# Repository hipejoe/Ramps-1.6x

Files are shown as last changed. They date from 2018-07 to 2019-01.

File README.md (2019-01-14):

Ramps-1.6 or so
===========

forked from ultimachine/Ramps 1.4

terminated AUX doe to space

added libs for tmc2130 watterot with conf0 installed 
add E2
chanded libs f tmc2130 to not use space of unused headers
added supression to endstops but removed 2nd endstop for axis (has tmc2130 so only Z and probe may need one.
re added 2servos
upgraded to 4thermoistors

integrated my previous fan extendr to 5 external outputs
removed VIN (toDO! check arduinos power consumption etc)
changed package or reset + external reset 

changed few Packages to match order
Orderd First Batch PCBs to test

RAMPS 1.6.3 
Got one wirestumb on Zmin fixed
Changed Pins Back to HWSPI 
Added I2C pin Header and HW SPI breakout
added 5vin 

Current status: all up and running thermistors are and endstops are "noisefree" printe is running it for 5month now, got some PCBs left..

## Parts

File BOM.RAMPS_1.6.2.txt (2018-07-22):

Stückliste exportiert aus D:/Documents/PCB/eagle/eagle/proj/RAMTPB/Ramps-1.4.2-master/RAMPS_1.6.2.sch am 22.07.2018 23:47

Qty Value               Device                  Package                      Parts                         Description                                                                                                     MF MPN OC_FARNELL OC_NEWARK SF_ID     SPICEPREFIX
4                       2,15/1,0                2,15/1,0                     +12, +24, G12, GND            THROUGH-HOLE PAD                                                                                                                                                 
3                       3PIN-HEADER             3PIN-HEADER                  X-, Y-, Z-                    PIN HEADER                                                                                                                                                       
3                       CONN_022.54MM_SCREWTERM 1X02_2.54_SCREWTERM          HEAT1, HEAT2, HEAT3           Multi connection point. Often used as Generic Header-pin footprint for 0.1 inch spaced/style header connections                                                  
4                       CONN_02LOCK             1X02_LOCK                    T0, T1, T2, T3                Multi connection point. Often used as Generic Header-pin footprint for 0.1 inch spaced/style header connections                                                  
6                       CONN_02POLAR_LOCK       MOLEX-1X2_LOCK               EX0, EX1, EX2, EX3, EX4, RSET Multi connection point. Often used as Generic Header-pin footprint for 0.1 inch spaced/style header connections                             PRT-09918 B          
2                       CONN_03                 1X03                         SERV0, SERV1                  Multi connection point. Often used as Generic Header-pin footprint for 0.1 inch spaced/style header connections                                                  
5                       NMOSSOT223              SOT223                       TEX0, TEX1, TEX2, TEX3, TEX4  MOS FET                                                                                                                unknown    unknown             J          
3   1.8K                R-US_R1206              R1206                        R23, R24, R25                 RESISTOR, American symbol                                                                                                                                        
5   1.8K                R-US_R1206              R1206                        R20, R28, R31, R34, R37       RESISTOR, American symbol                                                                                                                             R          
5   10                  R-US_R1206              R1206                        R18, R26, R29, R32, R35       RESISTOR, American symbol                                                                                                                             R          
1   100K                R-US_R1206              R1206                        R19                           RESISTOR, American symbol                                                                                                                             L          
4   100K                R-US_R1206              R1206                        R27, R30, R33, R36            RESISTOR, American symbol                                                                                                                             R          
3   100k                R-US_R1206              R1206                        R2, R4, R9                    RESISTOR, American symbol                                                                                                                                        
1   100nF               C-EUC1206               C1206                        C2                            CAPACITOR, European symbol                                                                                                                                       
7   100uF               CPOL-US153CLV-0605      153CLV-0605                  C3, C4, C6, C7, C9, C10, C17  POLARIZED CAPACITOR, American symbol                                                                                                                             
6   10k                 R-US_R1206              R1206                        R3, R5, R6, R8, R10, R16      RESISTOR, American symbol                                                                                                                                        
3   10r                 R-US_R1206              R1206                        R13, R14, R15                 RESISTOR, American symbol                                                                                                                                        
3   10uF                C-EUC1206               C1206                        C11, C13, C15                 CAPACITOR, European symbol                                                                                                                                       
4   10uF                CPOL-US153CLV-0405      153CLV-0405                  C1, C5, C8, C12               POLARIZED CAPACITOR, American symbol                                                                                                                             
1   1K                  R-US_R1206              R1206                        R12                           RESISTOR, American symbol                                                                                                                                        
2   1N4004              1N4004                  DO41-10                      D2, D3                        DIODE                                                                                                                                                            
4   4.7K                R-US_R1206              R1206                        R1, R7, R11, R17              RESISTOR, American symbol                                                                                                                                        
1   ARDUINOSHIELD       ARDUINOSHIELD           REPRAPJR_ARDUINO_MEGA_SHIELD U$1                           aus schaltplan kopierte version von amega                                                                                                                        
2   SMD-AUTOMOTIVE-FUSE SMD-AUTOMOTIVE-FUSE     BLADEFUSE                    F1, F2                        Surface mount fuse holder for kfz blade fuses                                                                                                                    
3   STP55NF06L          IRF512                  TO220BV                      Q1, Q2, Q3                    N-CHANNEL MOS FET                                                                                                                                                
6   TMC2130DIAG         TMC2130DIAG             TMC2130DIAG0                 E0, E1, E2, X, Y, Z                                                                                                                                                                            
1   green               LEDCHIPLED_1206         CHIPLED_1206                 LED1                          LED                                                                                                                                                              
3   red                 LEDCHIPLED_1206         CHIPLED_1206                 LED10, LEDD8, LEDD9           LED                                                                                                                                                              
5   red                 LEDCHIPLED_1206         CHIPLED_1206                 LED5, LED6, LED7, LED8, LED9  LED                                                                                                                                                   L          
1   reset               SKHMPWE010              SKHMPXE010                   S2                            6.2 X 6.5mm TACT Switch (SMD)

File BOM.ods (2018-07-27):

Qty | Value | Device | Package | Parts names | artNR | wo
4 |  | 2,15/1,0 | 2,15/1,0 | +12, +24, G12, GND
3 |  | 3PIN-HEADER | 3PIN-HEADER | X-, Y-, Z-
3 |  | CONN_022.54MM_SCREWTERM | 1X02_2.54_SCREWTERM | HEAT1, HEAT2, HEAT3
4 |  | CONN_02LOCK | 1X02_LOCK | T0, T1, T2, T3
6 |  | CONN_02POLAR_LOCK | MOLEX-1X2_LOCK | EX0, EX1, EX2, EX3, EX4, RSET
2 |  | CONN_03 | 1X03 | SERV0, SERV1
5 |  | NMOSSOT223 | SOT223 | TEX0, TEX1, TEX2, TEX3, TEX4 | ZVN 2106 G | rs | 0,45 | 2,25
8 | 1.8K | R-US_R1206 | R1206 | R20, R23, R24, R25, R28, R31, R34, R37 | RND 1206 1 1,8K | rs | 0,02 | 0,16
8 | 10ohm | R-US_R1206 | R1206 | R18, R26, R29, R32, R35 | RND 1206 1 10 | rs | 0,02 | 0,16
6 | 10k | R-US_R1206 | R1206 | R3, R5, R6, R8, R10, R16 | RND 1206 1 10K | rs | 0,02 | 0,12
4 | 4.7K | R-US_R1206 | R1206 | R1, R7, R11, R17 | RND 1206 1 4,7K | rs | 0,02 | 0,08
1 | 1K | R-US_R1206 | R1206 | R12 | RND 1206 1 1,1K | rs | 0,02 | 0,02
8 | 100K | R-US_R1206 | R1206 | R19, R27, R30, R33, R36 | RND 1206 1 100k | rs | 0,02 | 0,16
1 | 100nF | C-EUC1206 | C1206 | C2 | X7R 1206FCF 100N | rs | 0,04 | 0,04
7 | 100uF | CPOL-US153CLV-0605 | 153CLV-0605 6,3x5,6 | C3, C4, C6, C7, C9, C10, C17 | HA-V 100U 35 | rs | 0,28 | 1,96
3 | 10uF | C-EUC1206 | C1206 | C11, C13, C15 | Y5V 1206 DC 10U | rs | 0,04 | 0,12
4 | 10uF | CPOL-US153CLV-0405 | 153CLV-0405 4+5,6mm | C1, C5, C8, C12 | HA-V 10U 35-2 | rs | 0,16 | 0,64
2 | 1N4004 | 1N4004 | DO201 | D2, D3 | UF 5404 | rs | 0,15 | 0,3
1 | ARDUINOSHIELD | ARDUINOSHIELD | REPRAPJR_ARDUINO_MEGA_SHIELD | U$1 |  |  |  | 0
2 | SMD-AUTOMOTIVE-FUSEREICHELTVARIANTE | SMD-AUTOMOTIVE-FUSEREICHELTVARIANTE | RS-SMDFUSE | F1, F2 | IMAXX H1810-2X4 | rs | 0,93 | 1,86
3 | STP55NF06L | IRF512 | TO220BV | Q1, Q2, Q3 | IRLB 8721 | rs | 0,61 | 1,83
6 | TMC2130DIAG | TMC2130DIAG | TMC2130DIAG0 | E0, E1, E2, X, Y, Z |  |  |  | 0
1 | green | LEDCHIPLED_1206 | CHIPLED_1206 | LED1 | RND 135-00053 | rs | 0,06 | 0,06
8 | red | LEDCHIPLED_1206 | CHIPLED_1206 | LED5, LED6, LED7, LED8, LED9, LED10, LEDD8, LEDD9 | RND 135-00054 | rs | 0,06 | 0,48
1 | reset | SKHMPWE010 | SKHMPXE010 | S2 | TASTER 9315 | rs | 0,16 | 0,16
 |  |  |  |  |  |  |  | 10,4

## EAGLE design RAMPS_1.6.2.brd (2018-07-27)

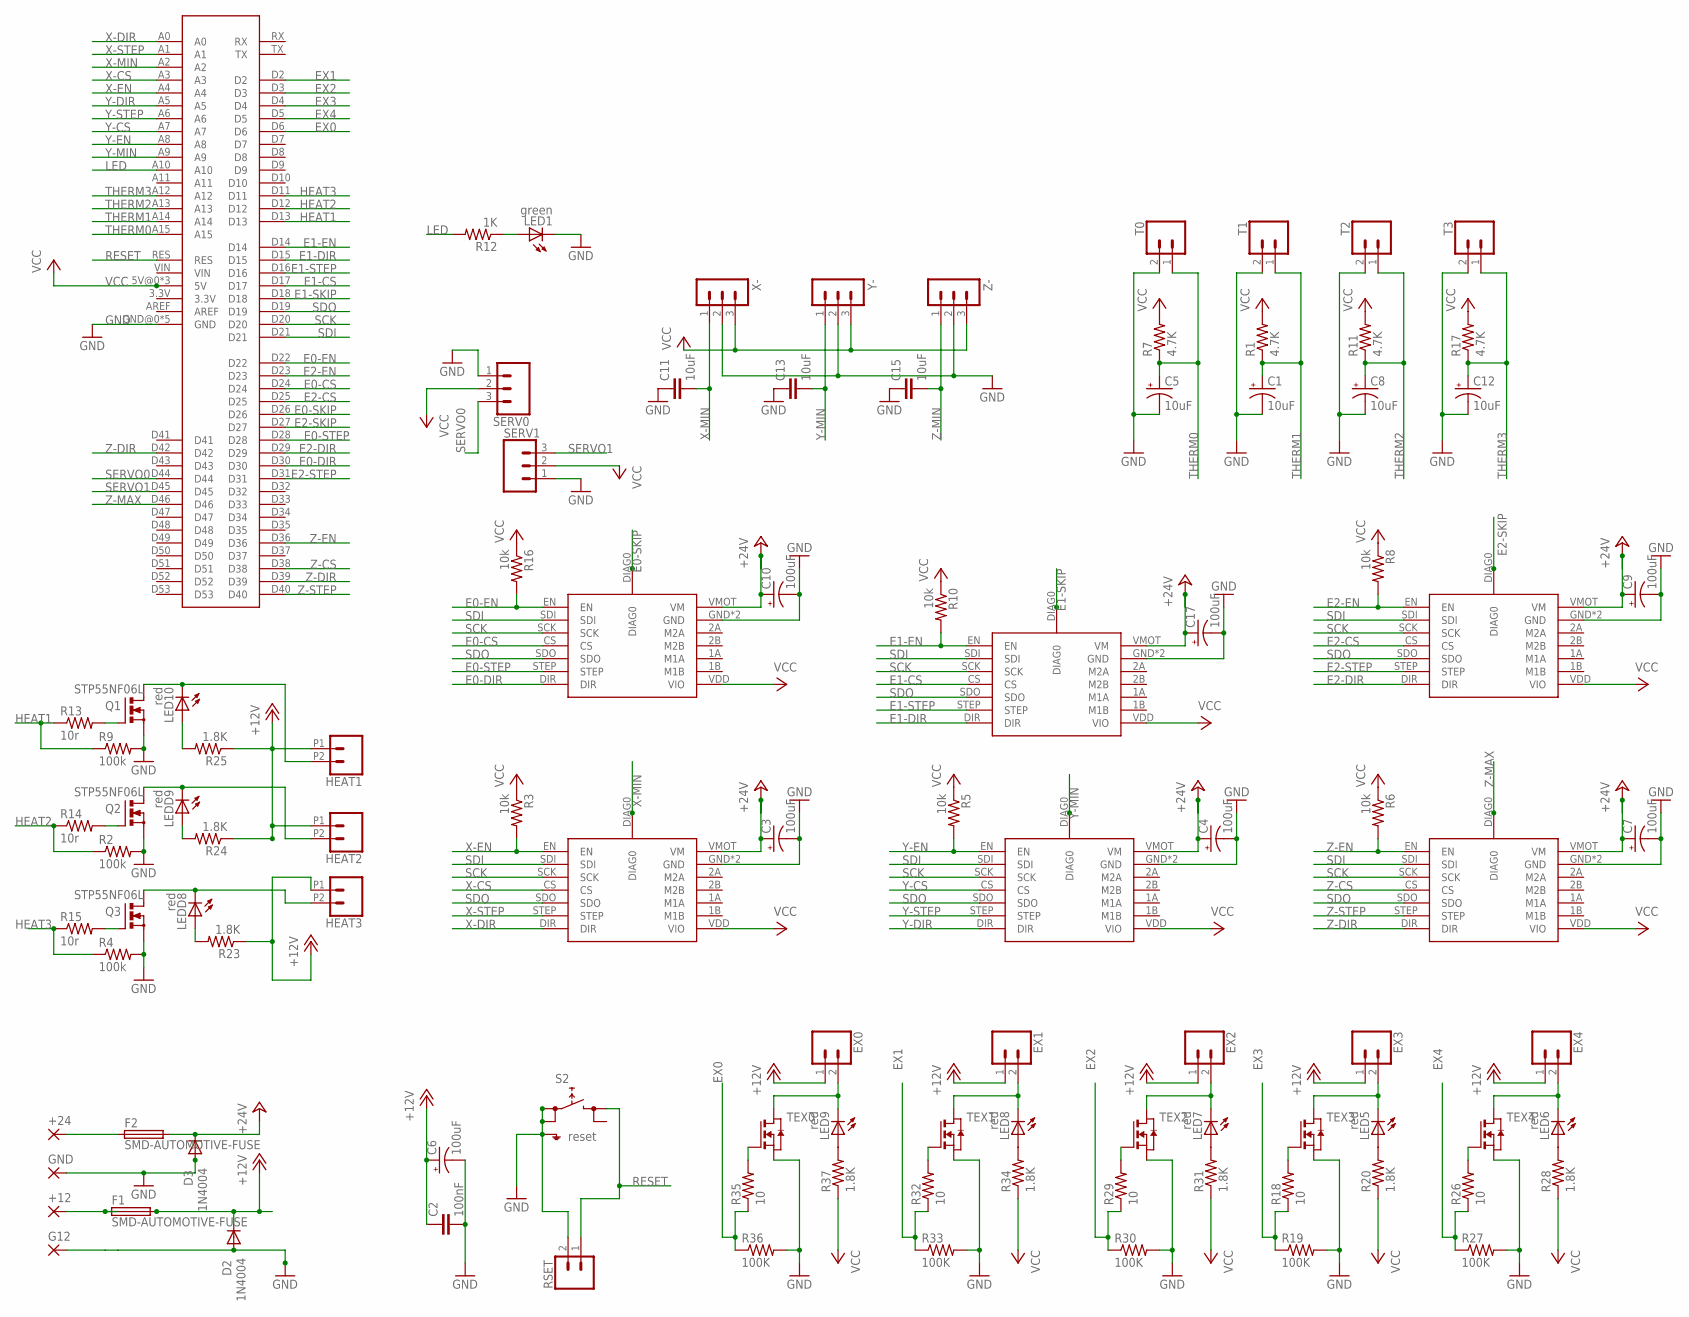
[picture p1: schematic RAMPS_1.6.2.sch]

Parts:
+12, +24: 2,15/1,0
C1, C5, C8, C12: 10uF; 153CLV-0405
C2: 100nF; C1206
C3, C4, C6, C7, C9, C10, C17: 100uF; 153CLV-0605
C11, C13, C15: 10uF; C1206
D2, D3: 1N4004; DO41-10
E0, E1, E2: TMC2130DIAG; TMC2130DIAG0
EX0, EX1, EX2, EX3, EX4: CONN_02POLAR_LOCK; MOLEX-1X2_LOCK
F1, F2: SMD-AUTOMOTIVE-FUSE; BLADEFUSE
G12: 2,15/1,0
GND: 2,15/1,0
HEAT1, HEAT2, HEAT3: CONN_022.54MM_SCREWTERM; 1X02_2.54_SCREWTERM
LED1: green; CHIPLED_1206
LED5, LED6, LED7, LED8, LED9, LED10: red; CHIPLED_1206
LEDD8, LEDD9: red; CHIPLED_1206
Q1, Q2, Q3: STP55NF06L; TO220BV
R1, R7, R11, R17: 4.7K; R1206
R2, R4, R9: 100k; R1206
R3, R5, R6, R8, R10, R16: 10k; R1206
R12: 1K; R1206
R13, R14, R15: 10r; R1206
R18, R26, R29, R32, R35: 10; R1206
R19, R27, R30, R33, R36: 100K; R1206
R20, R23, R24, R25, R28, R31, R34, R37: 1.8K; R1206
RSET: CONN_02POLAR_LOCK; MOLEX-1X2_LOCK
S2: reset; SKHMPXE010
SERV0, SERV1: CONN_03; 1X03
T0, T1, T2, T3: CONN_02LOCK; 1X02_LOCK
TEX0, TEX1, TEX2, TEX3, TEX4: NMOSSOT223; SOT223
U$1: ARDUINOSHIELD; REPRAPJR_ARDUINO_MEGA_SHIELD
X: TMC2130DIAG; TMC2130DIAG0
X-: 3PIN-HEADER
Y: TMC2130DIAG; TMC2130DIAG0
Y-: 3PIN-HEADER
Z: TMC2130DIAG; TMC2130DIAG0
Z-: 3PIN-HEADER

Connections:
+12V: C2.1, C6.+, D2.C, EX0.1, EX1.1, EX2.1, EX3.1, EX4.1, F1.2, F1.P$5, F1.P$6, F1.P$7, F1.P$8, HEAT1.P1 (1), HEAT2.P1 (1), HEAT3.P1 (1), R23.1, R24.1, R25.1
+24V: C3.+, C4.+, C7.+, C9.+, C10.+, C17.+, D3.C, E0.VMOT (VM), E1.VMOT (VM), E2.VMOT (VM), F2.2, F2.P$5, F2.P$6, F2.P$7, F2.P$8, X.VMOT (VM), Y.VMOT (VM), Z.VMOT (VM)
E0-CS: E0.CS, U$1.D24
E0-DIR: E0.DIR, U$1.D30
E0-EN: E0.EN, R16.2, U$1.D22
E0-SKIP: E0.DIAG0, U$1.D26
E0-STEP: E0.STEP, U$1.D28
E1-CS: E1.CS, U$1.D17
E1-DIR: E1.DIR, U$1.D15
E1-EN: E1.EN, R10.2, U$1.D14
E1-SKIP: E1.DIAG0, U$1.D18
E1-STEP: E1.STEP, U$1.D16
E2-CS: E2.CS, U$1.D25
E2-DIR: E2.DIR, U$1.D29
E2-EN: E2.EN, R8.2, U$1.D23
E2-SKIP: E2.DIAG0, U$1.D27
E2-STEP: E2.STEP, U$1.D31
EX0: R35.1, R36.1, U$1.D6
EX1: R32.1, R33.1, U$1.D2
EX2: R29.1, R30.1, U$1.D3
EX3: R18.1, R19.1, U$1.D4
EX4: R26.1, R27.1, U$1.D5
GND: C1.-, C2.2, C3.-, C4.-, C5.-, C6.-, C7.-, C8.-, C9.-, C10.-, C11.1, C12.-, C13.1, C15.1, C17.-, D2.A, D3.A, E0.GND, E0.GND@0 (GND), E1.GND, E1.GND@0 (GND), E2.GND, E2.GND@0 (GND), G12.1, GND.1, LED1.C, Q1.S, Q2.S, Q3.S, R2.2, R4.2, R9.2, R19.2, R27.2, R30.2, R33.2, R36.2, RSET.2, S2.1 (1.1), S2.2 (1.2), SERV0.1, SERV1.1, T0.2, T1.2, T2.2, T3.2, TEX0.3 (S), TEX1.3 (S), TEX2.3 (S), TEX3.3 (S), TEX4.3 (S), U$1.GND@0 (GND), U$1.GND@1 (GND), U$1.GND@2 (GND), U$1.GND@3 (GND), U$1.GND@4 (GND), X.GND, X.GND@0 (GND), X-.2, Y.GND, Y.GND@0 (GND), Y-.2, Z.GND, Z.GND@0 (GND), Z-.2; also elsewhere on the board
HEAT1: R9.1, R13.1, U$1.D13
HEAT2: R2.1, R14.1, U$1.D12
HEAT3: R4.1, R15.1, U$1.D11
LED: R12.2, U$1.A10
unnamed: HEAT2.P2 (2), LEDD9.C, Q2.D
unnamed: R18.2, TEX3.1 (G)
unnamed: HEAT1.P2 (2), LED10.C, Q1.D
unnamed: EX3.2, LED5.C, TEX3.2 (D), TEX3.4 (D)
unnamed: LED5.A, R20.2
unnamed: EX2.2, LED7.C, TEX2.2 (D), TEX2.4 (D)
unnamed: R26.2, TEX4.1 (G)
unnamed: EX4.2, LED6.C, TEX4.2 (D), TEX4.4 (D)
unnamed: LEDD8.A, R23.2
unnamed: LED6.A, R28.2
unnamed: R29.2, TEX2.1 (G)
unnamed: LED7.A, R31.2
unnamed: R32.2, TEX1.1 (G)
unnamed: EX1.2, LED8.C, TEX1.2 (D), TEX1.4 (D)
unnamed: LED8.A, R34.2
unnamed: R35.2, TEX0.1 (G)
unnamed: LEDD9.A, R24.2
unnamed: LED1.A, R12.1
unnamed: Q2.G, R14.2
unnamed: Q1.G, R13.2
unnamed: Q3.G, R15.2
unnamed: LED10.A, R25.2
unnamed: HEAT3.P2 (2), LEDD8.C, Q3.D
unnamed: +24.1, F2.1, F2.P$1, F2.P$2, F2.P$3, F2.P$4
unnamed: +12.1, F1.1, F1.P$1, F1.P$2, F1.P$3, F1.P$4
unnamed: EX0.2, LED9.C, TEX0.2 (D), TEX0.4 (D)
unnamed: LED9.A, R37.2
RESET: RSET.1, S2.3 (2.1), U$1.RES; also elsewhere on the board
SCK: E0.SCK, E1.SCK, E2.SCK, U$1.D20, X.SCK, Y.SCK, Z.SCK
SDI: E0.SDI, E1.SDI, E2.SDI, U$1.D21, X.SDI, Y.SDI, Z.SDI
SDO: E0.SDO, E1.SDO, E2.SDO, U$1.D19, X.SDO, Y.SDO, Z.SDO
SERVO0: SERV0.3, U$1.D44
SERVO1: SERV1.3, U$1.D45
THERM0: C5.+, R7.1, T0.1, U$1.A15
THERM1: C1.+, R1.1, T1.1, U$1.A14
THERM2: C8.+, R11.1, T2.1, U$1.A13
THERM3: C12.+, R17.1, T3.1, U$1.A12
VCC: E0.VDD (VIO), E1.VDD (VIO), E2.VDD (VIO), R1.2, R3.1, R5.1, R6.1, R7.2, R8.1, R10.1, R11.2, R16.1, R17.2, R20.1, R28.1, R31.1, R34.1, R37.1, SERV0.2, SERV1.2, U$1.5V@0 (5V), U$1.5V@1 (5V), U$1.5V@2 (5V), X.VDD (VIO), X-.3, Y.VDD (VIO), Y-.3, Z.VDD (VIO), Z-.3
X-CS: U$1.A3, X.CS
X-DIR: U$1.A0, X.DIR
X-EN: R3.2, U$1.A4, X.EN
X-MIN: C11.2, U$1.A2, X.DIAG0, X-.1
X-STEP: U$1.A1, X.STEP
Y-CS: U$1.A7, Y.CS
Y-DIR: U$1.A5, Y.DIR
Y-EN: R5.2, U$1.A8, Y.EN
Y-MIN: C13.2, U$1.A9, Y.DIAG0, Y-.1
Y-STEP: U$1.A6, Y.STEP
Z-CS: U$1.D38, Z.CS
Z-DIR: U$1.D39, U$1.D42, Z.DIR
Z-EN: R6.2, U$1.D36, Z.EN
Z-MAX: U$1.D46, Z.DIAG0
Z-MIN: C15.2, Z-.1
Z-STEP: U$1.D40, Z.STEP

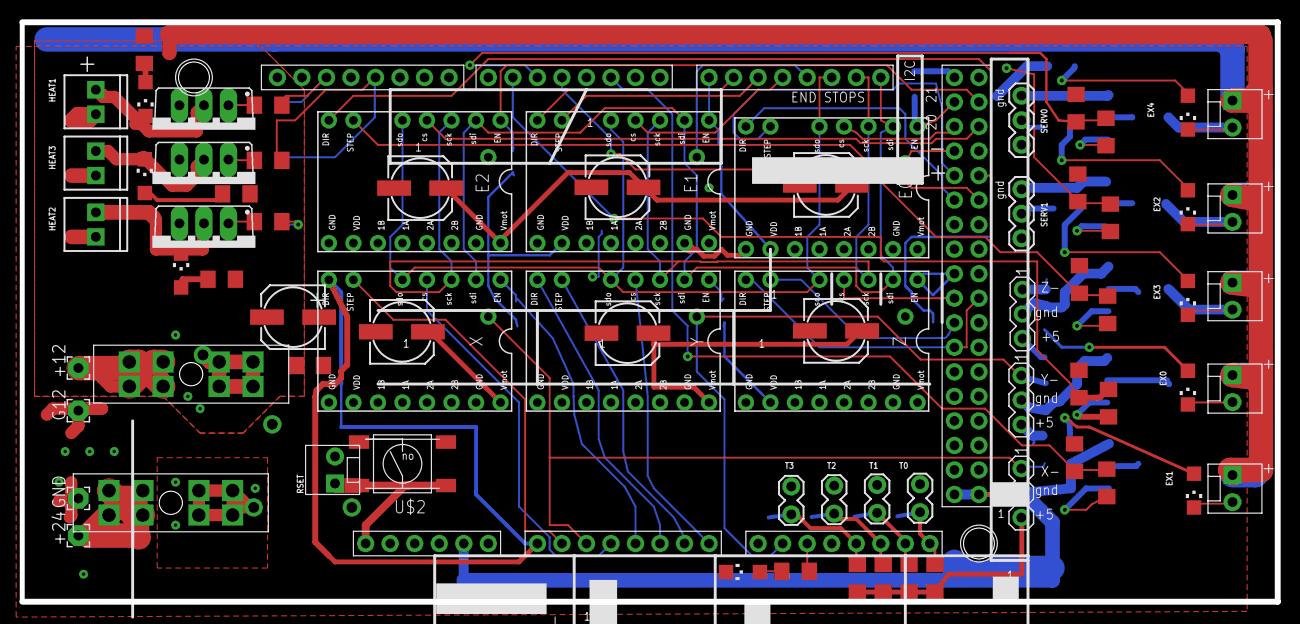
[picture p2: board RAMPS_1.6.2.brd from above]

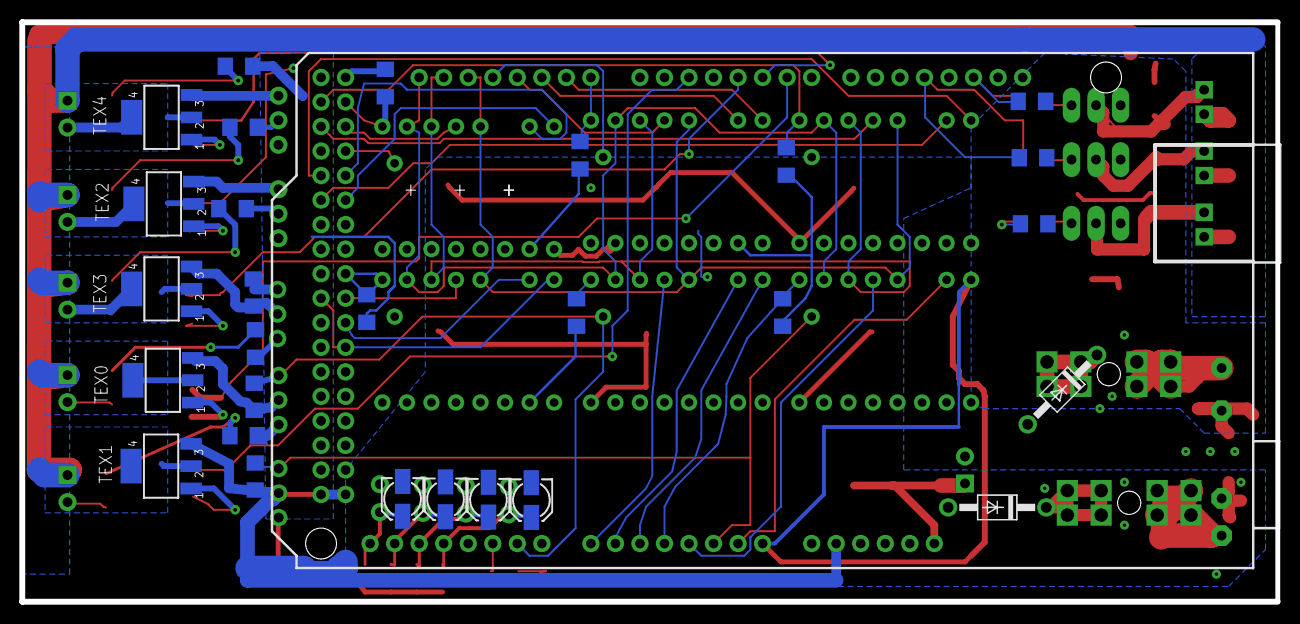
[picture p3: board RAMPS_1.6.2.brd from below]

Board: 4 copper layers, 130.0 x 60.0 mm, 101 parts (28 on the bottom side), 81 nets.

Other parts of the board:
U$2: RS-TASTER; RS-SWITCH

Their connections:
GND: U$2.P$1, U$2.P$2; also elsewhere on the board
RESET: U$2.P$3, U$2.P$4; also elsewhere on the board

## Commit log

2018-07-18 add new files from last few months
    [RAMPS_1.6.2.brd, RAMPS_1.6.2.sch]
2018-07-18 added images of current copper.
2018-07-22 BOM added
2018-07-22 changed package to 1206 on R and C
    [RAMPS_1.6.2.brd, RAMPS_1.6.2.sch]
2018-07-27 added BOM included Prices
    can all be ordered via Reichelt
    [BOM.ods]
2018-07-27 changed few componments for Order
    [RAMPS_1.6.2.brd]
2018-08-02 Gerbers for first produktion

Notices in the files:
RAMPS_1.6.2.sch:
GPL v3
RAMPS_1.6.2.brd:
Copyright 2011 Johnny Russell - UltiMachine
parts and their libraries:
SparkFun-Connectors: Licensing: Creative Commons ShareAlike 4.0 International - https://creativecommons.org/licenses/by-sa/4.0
